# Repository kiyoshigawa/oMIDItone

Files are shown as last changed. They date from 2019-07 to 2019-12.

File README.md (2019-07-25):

This is a project that takes an otamatone (https://otamatone.com/) and hijacks the control using digital potentiometers and a Teensy running USB MIDI libraries to turn it into a MIDI instrument.

The Controller PCB files currently use optoisolators. This design does not work correctly. I manually replaced the optoisolators with darlington NPN transistors, and that led to everything functioning as intended. I plan to revisit the PCB ocne I've tested the advanced features of the board (such as the servo control for opening the mouths, and the addressable LED lighting for the heads) to avoid needing more revisions.

The otamatone has had the touch-pot 'neck' removed and replaced with a connection to two MCP4151 digital potentiometers. I also had to connect two wires to the speaker outputs to get feedback on the frequency being played as the circuit is unstable over time and I could not map a resistance value to a given note accurately and reliably. I ended up removing the original PCBs from the heads and locating them centrally on my controller PCB to make wiring the heads and replacing damaged controllers easier. 

The current revision of the code is working with basic MIDI functionality, including note on, note off, and pitch bend. The pitch bending currently applies to every note currently being played. I intend to change it so that the pitch bend will apply to all the notes only on the MIDI channel it was sent on. This will allow multi-track MIDI files to send each track on a different channel so pitch bend will not effect all the tracks simultaneously. As far as I am aware, there is no way to differentiate tracks once the note messages are sent over MIDI if they are all sending to the same MIDI device, so per-track pitch bend is the best I can hope for given my single MIDI controller setup.

My goal is to finish the design and get all my planned features working with the current PCB, and then release a final version of the code and PCB for anyone who wants to follow in my crazy footsteps.

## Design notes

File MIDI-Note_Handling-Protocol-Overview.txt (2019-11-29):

This is intended to be a general overview explaining the logic in how the oMIDItone handles selecting which MIDI notes to play.

The oMIDItone will make an array of all currently-on notes. This will be updated by MIDI Note-On and Note-Off messages.
Any pitch-bending will apply to all notes without exception.

There are several scenarios that can occur here. Unchanging parameters:
    -There are 127 MIDI notes that can be played, any of which could be on.
    -There are up to 6 oMIDItones available at any given time, sometimes less.
    -You can use oMIDItone.can_play_note() to see if a specific note can be played by any specific head.
    -This results in a set of oMIDItones capable of playing a specific note, from 0-6 possible choices.

So we've got a set of notes, between 0-127, we should be playing, and we've got between 0-6 oMIDItones that can play any given note.

We need to decide which notes to play somehow, and which head to play any given note on.

Scenarios that can arise:
    1. -Notes exist that cannot be played by any heads.
    2. -Less notes than heads, all notes can be played on available heads.
    3. -Less notes than heads, some notes cannot be played on available heads. We will need to select which notes get played on which heads.
    4. -More notes than heads, all within the range of available heads. We will need to select which notes get played on which heads.

We should add a state variable that causes the logic to update only when a note value has changed to save processing time, as this seems like it could get a little complicated.

Solutions:
    1. -Trivially, we can map the max and min notes across all heads and ignore any notes outside this range to save time in for loops constantly checking heads to see what they can play. This should be done during the setup, after all the initializations are complete.
    2. -We check to see that there are only n notes on and >n heads capable of playing all the notes. We need to confirm there is no overlap or multiple notes that can be played on a specific head only and then we can assign heads without worry.
    3. and 4. -This is where things get more complicted. I see there are two paradigms we could follow for these cases to decide how to handle notes:
        A. -The first note that was pressed gets priority over newer notes if a decision has to be made to drop a note.
        B. -The most recently pressed note gets priority over older notes if a decision has to be made to drop a note.
            -B seems to make more sense, as Sodar pointed out that long chord sustains would override the melody bits.

Either way, it sounds like I will need to record the time of the note_on messages somehow so that I can iterate through the notes in the order they were sent to decide which way to operate. Current code only has an array that notes which notes are on or off, it might make sense to do this as an array that holds only the currently-on notes per MIDI, and keeps them in the order they were received. You can also remove notes from the array and shift the remaining notes when receiving note_off commands, adding them to the end of the array. This saves us from having to track the exact time the MIDI messages were received, and keeps things in chronological order.

Also, the chronological array has the advantage that if a note ends and a head that was in use becomes available, a different note can resume even if it was overridden previously.

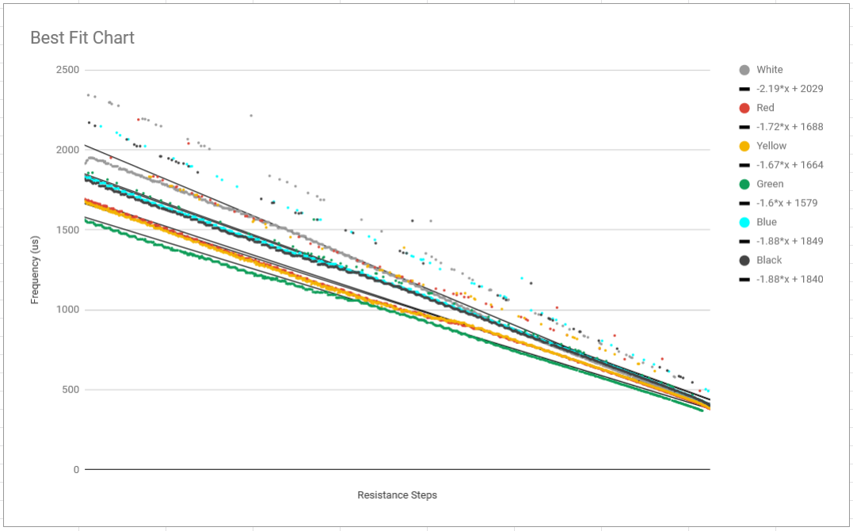
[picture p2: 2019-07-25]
Controller PCB/Reverse Engineering Original Board/Best Fit Chart.PNG

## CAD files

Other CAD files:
Face_Grabber/arm_testing_recover.dwg
Face_Grabber/Light Box Laser Layout.dwg
Face_Grabber/Electronics Backplate.dwg
Face_Grabber/Face-Grabber-FInal.dwg

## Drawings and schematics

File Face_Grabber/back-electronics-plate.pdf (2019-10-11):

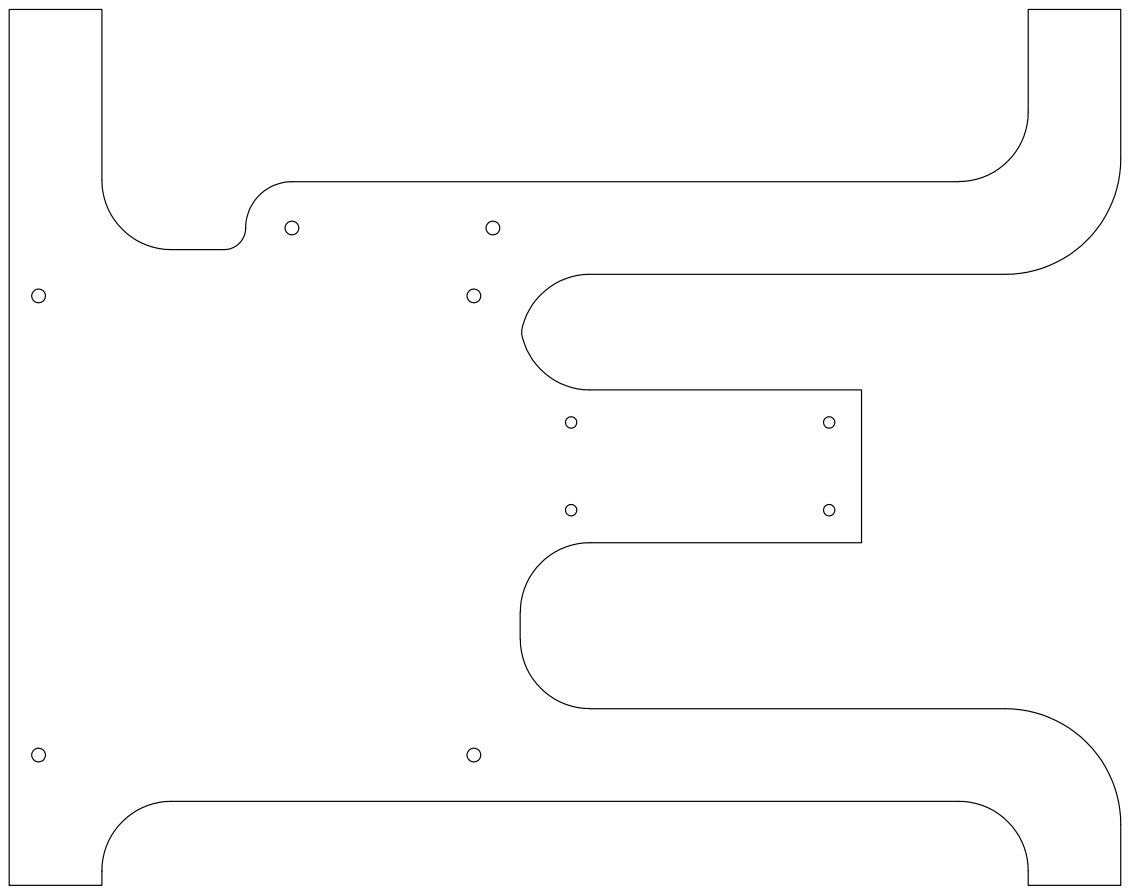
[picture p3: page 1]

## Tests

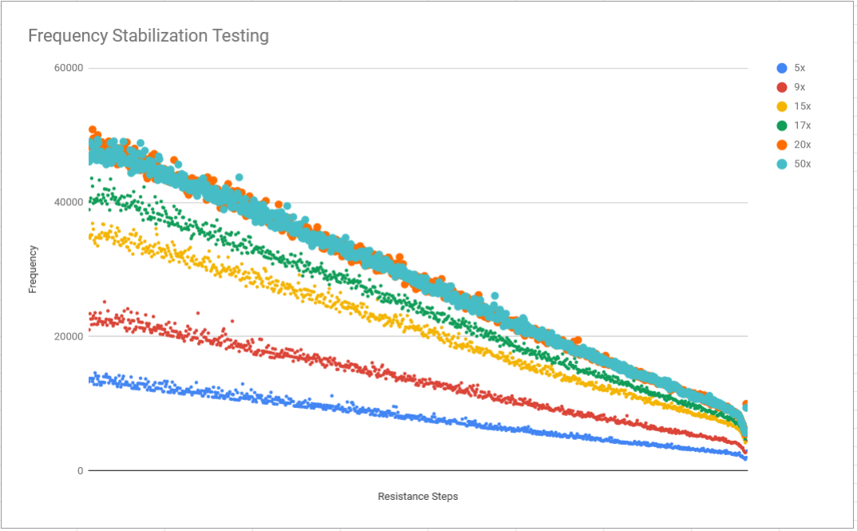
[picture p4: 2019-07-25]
Controller PCB/Reverse Engineering Original Board/Frequency Stabilization Testing.PNG

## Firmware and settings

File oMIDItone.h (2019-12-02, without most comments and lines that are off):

#define OMIDITONE_H
#include <Arduino.h>
#include <SPI.h>
#include "ADC-master/ADC.h"
#include <i2c_t3.h>
#include "Adafruit_PWMServoDriver.h"
#include "lighting_control.h"
#define OMIDITONE_DEBUG
#define FREQUENCY_CORRECTION_DEFAULT_ENABLE_STATE true
#define SERVO_DEFAULT_ENABLE_STATE true
#define NUM_OMIDITONES 6
#define NO_NOTE 128
#define NO_CHANNEL 17
#define NO_RESISTANCE -1
#define NOTE_A 440
#define NUM_MIDI_NOTES 128
#define NUM_MIDI_CHANNELS 16
#define NUM_RESISTANCE_STEPS 765
#define RISING_EDGE_THRESHOLD 50
#define ALLOWABLE_NOTE_ERROR 1
#define DEFAULT_MIDI_PITCH_BEND_SEMITONES 2
#define DEFAULT_MIDI_PITCH_BEND_CENTS 0
#define MAX_PITCH_BEND_SEMITONES 24
#define MAX_PITCH_BEND_CENTS 99
#define ALLOWABLE_FREQUENCY_READING_VARIANCE 50
#define MIN_TIME_BETWEEN_RISING_EDGE_MEASUREMENTS 1
#define NOTE_WAIT_TIME 10
#define TIME_BETWEEN_FREQUENCY_CORRECTIONS 20
#define JITTER 1
#define NUM_FREQ_READINGS 5
#define INIT_MULTIPLIER 17
#define TIME_TO_WAIT_FOR_INIT 2000
#define TIME_TO_WAIT_FOR_STARTUP_TEST_SOUND 100
#define NOTE_TIMEOUT 2000
#define UNREASONABLY_LARGE_MULTIPLIER 2
#define CENTER_PITCH_BEND 0
#define MAX_FREQ 300
#define PCA9685_ADDRESS 0x41
#define PCA9685_FREQUENCY 240
#define PCA9685_OE_PIN 20
#define NUM_LEDS_PER_HEAD 18
#define TIME_BETWEEN_SERVO_MOVEMENTS 16
#define CENT_FREQUENCY_RATIO_MULTIPLIER 1000000
const uint32_t midi_freqs[NUM_MIDI_NOTES] = {122309, 115446, 108968, 102848, 97077, 91633, 86490, 81632, 77053, 72727, 68643, 64792, 61154, 57723, 54484, 51427, 48538, 45814, 43243, 40816, 38525, 36363, 34322, 32396, 30578, 28861, 27242, 25712, 24270, 22907, 21622, 20408, 19262, 18181, 17161, 16198, 15289, 14430, 13621, 12856, 12134, 11453, 10810, 10204, 9631, 9090, 8580, 8099, 7644, 7215, 6810, 6428, 6067, 5726, 5405, 5102, 4815, 4545, 4290, 4049, 3822, 3607, 3405, 3214, 3033, 2863, 2702, 2551, 2407, 2272, 2145, 2024, 1911, 1803, 1702, 1607, 1516, 1431, 1351, 1275, 1203, 1136, 1072, 1012, 955, 901, 851, 803, 758, 715, 675, 637, 601, 568, 536, 506, 477, 450, 425, 401, 379, 357, 337, 318, 300, 284, 268, 253, 238, 225, 212, 200, 189, 178, 168, 159, 150, 142, 134, 126, 119, 112, 106, 100, 94, 89, 84, 79};
const uint32_t cent_frequency_ratios[199] = {1058851, 1058240, 1057629, 1057018, 1056408, 1055798, 1055188, 1054579, 1053970, 1053361, 1052753, 1052145, 1051537, 1050930, 1050323, 1049717, 1049111, 1048505, 1047899, 1047294, 1046689, 1046085, 1045481, 1044877, 1044274, 1043671, 1043068, 1042466, 1041864, 1041262, 1040661, 1040060, 1039459, 1038859, 1038259, 1037660, 1037060, 1036462, 1035863, 1035265, 1034667, 1034070, 1033472, 1032876, 1032279, 1031683, 1031087, 1030492, 1029897, 1029302, 1028708, 1028114, 1027520, 1026927, 1026334, 1025741, 1025149, 1024557, 1023965, 1023374, 1022783, 1022192, 1021602, 1021012, 1020423, 1019833, 1019244, 1018656, 1018068, 1017480, 1016892, 1016305, 1015718, 1015132, 1014545, 1013959, 1013374, 1012789, 1012204, 1011619, 1011035, 1010451, 1009868, 1009285, 1008702, 1008120, 1007537, 1006956, 1006374, 1005793, 1005212, 1004632, 1004052, 1003472, 1002892, 1002313, 1001734, 1001156, 1000578, 1000000, 999423, 998845, 998269, 997692, 997116, 996540, 995965, 995390, 994815, 994240, 993666, 993092, 992519, 991946, 991373, 990801, 990228, 989657, 989085, 988514, 987943, 987373, 986803, 986233, 985663, 985094, 984525, 983957, 983388, 982821, 982253, 981686, 981119, 980552, 979986, 979420, 978855, 978289, 977725, 977160, 976596, 976032, 975468, 974905, 974342, 973779, 973217, 972655, 972093, 971532, 970971, 970410, 969850, 969290, 968730, 968171, 967612, 967053, 966494, 965936, 965379, 964821, 964264, 963707, 963151, 962594, 962039, 961483, 960928, 960373, 959818, 959264, 958710, 958157, 957603, 957050, 956498, 955945, 955393, 954842, 954290, 953739, 953188, 952638, 952088, 951538, 950989, 950439, 949891, 949342, 948794, 948246, 947698, 947151, 946604, 946058, 945511, 944965, 944420};
class oMIDItone {
	public:
		oMIDItone(uint16_t signal_enable_optoisolator, uint16_t speaker_disable_optoisolator, uint16_t cs1, uint16_t cs2, uint16_t feedback, uint16_t servo_l_channel, uint16_t servo_r_channel, uint16_t servo_l_min, uint16_t servo_l_max, uint16_t servo_r_min, uint16_t servo_r_max, uint16_t led_head_array[NUM_LEDS_PER_HEAD], Animation * head_animation);
		void init();
		void update();
		bool note_on(uint16_t note, uint16_t velocity, uint16_t channel);
		void note_off(uint16_t note);
		void set_pitch_bend(int16_t pitch_bend_value, uint8_t pitch_bend_channel);
		void set_max_pitch_bend(uint8_t semitones, uint8_t cents);
		void cancel_pitch_correction();
		void set_servos(uint16_t position);
		bool is_running();
		uint16_t currently_playing_note();
		uint16_t currently_playing_pitch_bend(uint16_t channel);
		void enable_pitch_correction();
		void disable_pitch_correction();
		void enable_servos();
		void disable_servos();
		Animation * animation;
	private:
		bool startup_test();
		void measure_frequency();
		void adjust_frequency();
		bool can_play_note(uint8_t note, int16_t pitch_bend);
		uint32_t pitch_adjusted_frequency(uint8_t note, int16_t pitch_bend);
		void servo_update();
		bool is_rising_edge();
		uint32_t average(unsigned long * array, uint16_t num_elements);
		uint16_t frequency_to_resistance(uint16_t frequency);
		void set_jitter_resistance(uint16_t resistance, uint16_t jitter);
		void set_resistance(uint16_t resistance);
		void set_pot(uint16_t CS_pin, uint16_t command_byte);
		bool had_successful_init;
		bool pitch_correction_is_enabled;
		bool servo_is_enabled;
		uint16_t current_note;
		uint16_t current_velocity;
		uint16_t current_channel;
		uint16_t min_note;
		uint16_t max_note;
		uint32_t measured_freqs[NUM_RESISTANCE_STEPS];
		uint32_t recent_freqs[NUM_FREQ_READINGS];
		uint16_t freq_reading_index;
		uint32_t current_freq;
		uint32_t current_desired_freq;
		uint32_t max_pitch_bend_offset;
		elapsedMicros last_rising_edge;
		elapsedMillis last_adjust_time;
		elapsedMillis last_stabilize_time;
		elapsedMillis note_start_time;
		elapsedMillis startup_stabilization_began;
		elapsedMillis last_frequency_measurement;
		uint16_t last_analog_read;
		int16_t current_oMIDItone_pitch_bend[NUM_MIDI_CHANNELS];
		uint16_t current_resistance;
		uint16_t signal_enable_optoisolator_pin;
		uint16_t speaker_disable_optoisolator_pin;
		uint16_t cs1_pin;
		uint16_t cs2_pin;
		uint16_t analog_feedback_pin;
		ADC *adc = new ADC();
		uint16_t l_channel;
		uint16_t r_channel;
		uint16_t l_min;
		uint16_t l_max;
		uint16_t r_min;
		uint16_t r_max;
		Adafruit_PWMServoDriver servo_controller = Adafruit_PWMServoDriver(PCA9685_ADDRESS);
		elapsedMillis last_servo_update;
		bool pitch_correction_has_been_compromised;
		uint16_t * led_position_array;
};

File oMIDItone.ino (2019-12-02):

/*
Author: kiyoshigawa
Start Date: 2018-03-18
Description:
Took an Otamatone, and replaced the pressure-sensitive variable resistor strip with some MCP4151 50kohm variable pots (2 in series) with a 220Ohm fixed resistor.
Then used a teensy LC MIDI library to control the resistance from the chips over SPI, and connected it to the otamatone, making a oMIDItone.

Update: 2019-03-23: converted the code into a class, rewrote everything to work with the class, can run up to 6 on a Teensy 3.2, only one on a Teensy LC due to lack of RAM.
Update: 2019-03-27: Got all the features working, should be a fully functional MIDI instrument, pending testing of analog read speeds keeping up with higher frequency notes when more than 2 oMIDItones are running. I only have 2 for testing atm, need to buy more.
Update: 2019-09-26: This is now configured (at least initially) for the fully functional v3 PCB, which includes servo face grabbers, LED lighting, and 6 heads. I also added support for per-channel pitch bending, so you can have a channel bend but not all the others with it. Any notes on the bent chanel will be bent as well, though. Working on timing for animation updates, and then I will need to improve the lighting and servo animations. Once those two things are done, I think we can call it stable and mark it as the official release.
Update 2019-11-10: Added MIDI functionality to control various aspects of the oMIDItone using CC messages, and offloaded the MIDI handling to the MIDI_control.h file.

*/

#include "oMIDItone.h"
#include <MIDI.h>
#include <Adafruit_NeoPixel.h>
#include "lighting_control.h"

//this will print messages on system startup and init
#define BOOT_DEBUG

//This will turn on/off the debug note messages when notes are added or removed via MIDI
//#define NOTE_DEBUG

//defines to make the head selection code more readable:
#define AVAILABLE true
#define NOT_AVAILABLE false

//This is the pulse offset in microseconds from the min value of the servo position to the max (i.e. fully open)
#define SERVO_MAX_OFFSET 220

//The next few #defines are for the Adafruit_Neopixel.h library stuff:
#define LED_TOTAL_NUM NUM_LEDS_PER_HEAD*NUM_OMIDITONES
#define LED_DATA_PIN 2
#define LED_COLOR_ORDER NEO_GRB
#define LED_SPEED NEO_KHZ800
#define LED_BRIGHTNESS 255

//This controls the lighting animation timing. 16667 ~= 60Hz, 33333 ~= 30Hz
#define TIME_BETWEEN_LIGHTING_UPDATES 33333

//these are default lighting info for the heads:
#define DEFAULT_BG_MODE LC_BG_RAINBOW_SLOW_ROTATE
#define DEFAULT_FG_MODE LC_FG_NONE
#define DEFAULT_TRIGGER_MODE LC_TRIGGER_COLOR_PULSE

#define DEFAULT_OM1_BG_RAINBOW 16
#define DEFAULT_OM2_BG_RAINBOW 17
#define DEFAULT_OM3_BG_RAINBOW 18
#define DEFAULT_OM4_BG_RAINBOW 19
#define DEFAULT_OM5_BG_RAINBOW 20
#define DEFAULT_OM6_BG_RAINBOW 21
#define DEFAULT_OM1_FG_RAINBOW 1
#define DEFAULT_OM2_FG_RAINBOW 1
#define DEFAULT_OM3_FG_RAINBOW 1
#define DEFAULT_OM4_FG_RAINBOW 1
#define DEFAULT_OM5_FG_RAINBOW 1
#define DEFAULT_OM6_FG_RAINBOW 1
#define DEFAULT_OM1_TRIGGER_RAINBOW 3
#define DEFAULT_OM2_TRIGGER_RAINBOW 5
#define DEFAULT_OM3_TRIGGER_RAINBOW 9
#define DEFAULT_OM4_TRIGGER_RAINBOW 13
#define DEFAULT_OM5_TRIGGER_RAINBOW 7
#define DEFAULT_OM6_TRIGGER_RAINBOW 11

// Pin and other head-specific Definitions
//om#_leds[] arrays are per head ordered from left to right, the first 6 are front leds, the next 6 are the back top, and the final 6 are the back bottom leds
//Red Head:
uint16_t om1_se_pin = 15;
uint16_t om1_sd_pin = 26;
uint16_t om1_cs1_pin = 17;
uint16_t om1_cs2_pin = 16;
uint16_t om1_analog_feedback_pin = A10;
uint16_t om1_l_min = 1390;
uint16_t om1_l_max = om1_l_min + SERVO_MAX_OFFSET;
uint16_t om1_r_min = 1340;
uint16_t om1_r_max = om1_r_min - SERVO_MAX_OFFSET;
uint16_t om1_l_channel = 0;
uint16_t om1_r_channel = 1;
uint16_t om1_leds[NUM_LEDS_PER_HEAD] = {12, 13, 14, 15, 16, 17, 95, 94, 93, 92, 91, 90, 84, 85, 86, 87, 88, 89};
//Yellow Head:
uint16_t om2_se_pin = 33;
uint16_t om2_sd_pin = 25;
uint16_t om2_cs1_pin = 22;
uint16_t om2_cs2_pin = 21;
uint16_t om2_analog_feedback_pin = A11;
uint16_t om2_l_min = 1475;
uint16_t om2_l_max = om1_l_min + SERVO_MAX_OFFSET;
uint16_t om2_r_min = 1430;
uint16_t om2_r_max = om1_r_min - SERVO_MAX_OFFSET;
uint16_t om2_l_channel = 2;
uint16_t om2_r_channel = 3;
uint16_t om2_leds[NUM_LEDS_PER_HEAD] = {23, 22, 21, 20, 19, 18, 59, 58, 57, 56, 55, 54, 48, 49, 50, 51, 52, 53};
//White Head:
uint16_t om3_se_pin = 24;
uint16_t om3_sd_pin = 30;
uint16_t om3_cs1_pin = 3;
uint16_t om3_cs2_pin = 23;
uint16_t om3_analog_feedback_pin = A13;
uint16_t om3_l_min = 1280;
uint16_t om3_l_max = om1_l_min + SERVO_MAX_OFFSET;
uint16_t om3_r_min = 1450;
uint16_t om3_r_max = om1_r_min - SERVO_MAX_OFFSET;
uint16_t om3_l_channel = 4;
uint16_t om3_r_channel = 5;
uint16_t om3_leds[NUM_LEDS_PER_HEAD] = {6, 7, 8, 9, 10, 11, 101, 100, 99, 98, 97, 96, 78, 79, 80, 81, 82, 83};
//Black Head:
uint16_t om4_se_pin = 10;
uint16_t om4_sd_pin = 29;
uint16_t om4_cs1_pin = 9;
uint16_t om4_cs2_pin = 8;
uint16_t om4_analog_feedback_pin = A12;
uint16_t om4_l_min = 1475;
uint16_t om4_l_max = om1_l_min + SERVO_MAX_OFFSET;
uint16_t om4_r_min = 1310;
uint16_t om4_r_max = om1_r_min - SERVO_MAX_OFFSET;
uint16_t om4_l_channel = 6;
uint16_t om4_r_channel = 7;
uint16_t om4_leds[NUM_LEDS_PER_HEAD] = {29, 28, 27, 26, 25, 24, 65, 64, 63, 62, 61, 60, 42, 43, 44, 45, 46, 47};
//Green Head:
uint16_t om5_se_pin = 32;
uint16_t om5_sd_pin = 28;
uint16_t om5_cs1_pin = 7;
uint16_t om5_cs2_pin = 6;
uint16_t om5_analog_feedback_pin = A14;
uint16_t om5_l_min = 1475;
uint16_t om5_l_max = om1_l_min + SERVO_MAX_OFFSET;
uint16_t om5_r_min = 1420;
uint16_t om5_r_max = om1_r_min - SERVO_MAX_OFFSET;
uint16_t om5_l_channel = 8;
uint16_t om5_r_channel = 9;
uint16_t om5_leds[NUM_LEDS_PER_HEAD] = {0, 1, 2, 3, 4, 5, 107, 106, 105, 104, 103, 102, 72, 73, 74, 75, 76, 77};
//Blue Head:
uint16_t om6_se_pin = 31;
uint16_t om6_sd_pin = 27;
uint16_t om6_cs1_pin = 5;
uint16_t om6_cs2_pin = 4;
uint16_t om6_analog_feedback_pin = A0;
uint16_t om6_l_min = 1335;
uint16_t om6_l_max = om1_l_min + SERVO_MAX_OFFSET;
uint16_t om6_r_min = 1410;
uint16_t om6_r_max = om1_r_min - SERVO_MAX_OFFSET;
uint16_t om6_l_channel = 14;
uint16_t om6_r_channel = 15;
uint16_t om6_leds[NUM_LEDS_PER_HEAD] = {35, 34, 33, 32, 31, 30, 71, 70, 69, 68, 67, 66, 36, 37, 38, 39, 40, 41};

//this array controls the type of notes being sent to each head on note_trigger events when they are active:
uint16_t note_trigger_type[NUM_OMIDITONES] = {	DEFAULT_TRIGGER_MODE,
												DEFAULT_TRIGGER_MODE,
												DEFAULT_TRIGGER_MODE,
												DEFAULT_TRIGGER_MODE,
												DEFAULT_TRIGGER_MODE,
												DEFAULT_TRIGGER_MODE};

//these are the Animation objects for the heads above - they will control the animation per-head.
Animation om1_animation = Animation(om1_leds, NUM_LEDS_PER_HEAD,
									(DEFAULT_BG_MODE | DEFAULT_FG_MODE),
									rb_array[DEFAULT_OM1_BG_RAINBOW],
									rb_array[DEFAULT_OM1_FG_RAINBOW],
									rb_array[DEFAULT_OM1_TRIGGER_RAINBOW],
									LC_DEFAULT_REFRESH_RATE);
Animation om2_animation = Animation(om2_leds, NUM_LEDS_PER_HEAD,
									(DEFAULT_BG_MODE | DEFAULT_FG_MODE),
									rb_array[DEFAULT_OM2_BG_RAINBOW],
									rb_array[DEFAULT_OM2_FG_RAINBOW],
									rb_array[DEFAULT_OM2_TRIGGER_RAINBOW],
									LC_DEFAULT_REFRESH_RATE);
Animation om3_animation = Animation(om3_leds, NUM_LEDS_PER_HEAD,
									(DEFAULT_BG_MODE | DEFAULT_FG_MODE),
									rb_array[DEFAULT_OM3_BG_RAINBOW],
									rb_array[DEFAULT_OM3_FG_RAINBOW],
									rb_array[DEFAULT_OM3_TRIGGER_RAINBOW],
									LC_DEFAULT_REFRESH_RATE);
Animation om4_animation = Animation(om4_leds, NUM_LEDS_PER_HEAD,
									(DEFAULT_BG_MODE | DEFAULT_FG_MODE),
									rb_array[DEFAULT_OM4_BG_RAINBOW],
									rb_array[DEFAULT_OM4_FG_RAINBOW],
									rb_array[DEFAULT_OM4_TRIGGER_RAINBOW],
									LC_DEFAULT_REFRESH_RATE);
Animation om5_animation = Animation(om5_leds, NUM_LEDS_PER_HEAD,
									(DEFAULT_BG_MODE | DEFAULT_FG_MODE),
									rb_array[DEFAULT_OM5_BG_RAINBOW],
									rb_array[DEFAULT_OM5_FG_RAINBOW],
									rb_array[DEFAULT_OM5_TRIGGER_RAINBOW],
									LC_DEFAULT_REFRESH_RATE);
Animation om6_animation = Animation(om6_leds, NUM_LEDS_PER_HEAD,
									(DEFAULT_BG_MODE | DEFAULT_FG_MODE),
									rb_array[DEFAULT_OM6_BG_RAINBOW],
									rb_array[DEFAULT_OM6_FG_RAINBOW],
									rb_array[DEFAULT_OM6_TRIGGER_RAINBOW],
									LC_DEFAULT_REFRESH_RATE);

//This is the LED strip object to control all the lighting on the board
Adafruit_NeoPixel strip = Adafruit_NeoPixel(LED_TOTAL_NUM, LED_DATA_PIN, LED_COLOR_ORDER + LED_SPEED);

//this is the lighting controller that will control the lighting updates on the above Adafruit_NeoPixel object's pixels:
LightingControl lc = LightingControl(&strip, LED_BRIGHTNESS);

//this is a timing variable to track lighting updates
elapsedMicros last_lighting_update;

//Using SPI0 on board, MOSI0 = 11, MISO0 = 12, and SCK0 = 13, which will blink the LED as it sends.

//declare the oMIDItone objects:
oMIDItone oms[NUM_OMIDITONES] = {
	oMIDItone(	om1_se_pin, om1_sd_pin, om1_cs1_pin, om1_cs2_pin, om1_analog_feedback_pin, om1_l_channel, 
				om1_r_channel, om1_l_min, om1_l_max, om1_r_min, om1_r_max, om1_leds, &om1_animation),
	oMIDItone(om2_se_pin, om2_sd_pin, om2_cs1_pin, om2_cs2_pin, om2_analog_feedback_pin, om2_l_channel, 
				om2_r_channel, om2_l_min, om2_l_max, om2_r_min, om2_r_max, om2_leds, &om2_animation),
	oMIDItone(om3_se_pin, om3_sd_pin, om3_cs1_pin, om3_cs2_pin, om3_analog_feedback_pin, om3_l_channel, 
				om3_r_channel, om3_l_min, om3_l_max, om3_r_min, om3_r_max, om3_leds, &om3_animation),
	oMIDItone(om4_se_pin, om4_sd_pin, om4_cs1_pin, om4_cs2_pin, om4_analog_feedback_pin, om4_l_channel, 
				om4_r_channel, om4_l_min, om4_l_max, om4_r_min, om4_r_max, om4_leds, &om4_animation),
	oMIDItone(om5_se_pin, om5_sd_pin, om5_cs1_pin, om5_cs2_pin, om5_analog_feedback_pin, om5_l_channel, 
				om5_r_channel, om5_l_min, om5_l_max, om5_r_min, om5_r_max, om5_leds, &om5_animation),
	oMIDItone(om6_se_pin, om6_sd_pin, om6_cs1_pin, om6_cs2_pin, om6_analog_feedback_pin, om6_l_channel, 
				om6_r_channel, om6_l_min, om6_l_max, om6_r_min, om6_r_max, om6_leds, &om6_animation)
};

//this is a variable storing the pitch bend value last received over MIDI:
//Note the teensy library uses a signed pitch bend centered on 0 instead of the MIDI standard of centering on 8192.
int16_t current_pitch_bend[NUM_MIDI_CHANNELS];

//this is an array that tracks whether a note is currently on or off.
uint8_t current_note_array[NUM_MIDI_NOTES];

//this will note the velocity that corresponds to the note array above.
uint8_t current_velocity_array[NUM_MIDI_NOTES];

//this will note the channel that corresponds to the note array above.
uint8_t current_channel_array[NUM_MIDI_NOTES];

//this tracks how many notes are in the array.
uint8_t num_current_notes = 0;

//this is a bool to let the controller know when it needs to reassign notes to the heads.
bool note_has_changed = false;

//this is a bool to let the controller know when it needs to reassign pitch bend to the heads.
bool pitch_has_changed = false;

//this updates all the heads when MIDI CC pitch bend messages are received:
bool pitch_bend_range_has_changed = false;

//these globals store the value of the pitch range in semitones and cents
uint8_t MIDI_max_pitch_bend_num_semitones = DEFAULT_MIDI_PITCH_BEND_SEMITONES;
uint8_t MIDI_max_pitch_bend_num_cents = DEFAULT_MIDI_PITCH_BEND_CENTS;

//This tracks the current head so the iteration isn't always in the same place.
int head_offset = 0;

//this controls whether lighting is enabled or not
bool lighting_is_enabled = true;

//this controls whether note on messages send triggers to the head that plays the note:
bool note_trigger_is_enabled = true;

//this is an array that is sorted in the order of the least recently used heads to the most recently used heads
//it allows for the least recently used heads to be selected first when deciding whish head will play a note
uint8_t head_order_array[NUM_OMIDITONES];
//this stores the state of the head order array until all notes are off, then it is pushed into the actual head order array.
uint8_t pending_head_order_array[NUM_OMIDITONES];

//Start the hardware MIDI:
MIDI_CREATE_INSTANCE(HardwareSerial, Serial1, MIDI);

//this is just a quick function to print the note array with some formatting:
void print_current_note_array(){
	#ifdef NOTE_DEBUG
		if(num_current_notes > 0){
			Serial.print("Notes: [");
			if(num_current_notes > 0){
				for(int i=0; i<num_current_notes-1; i++){
					Serial.print(current_note_array[i]);
					Serial.print(", ");
				}
			}
			Serial.print(current_note_array[num_current_notes-1]);
			Serial.println("]");
		} else {
			Serial.println("Notes: []");
		}
	#endif
}

//This will check to see if a note is in the current_note_array and return the position of the note if it finds one, or return NO_NOTE if it does not.
int check_note(uint8_t note){
	//Iterate through the array, and return the note position if it is found.
	if(num_current_notes == 0){
		return NO_NOTE;
	} else {
		for(int i=0; i<num_current_notes; i++){
			if(current_note_array[i] == note){
				return i;
			}
		}
		//if no note is found, return NO_NOTE;
		return NO_NOTE;
	}
}

//This will add a new note to the end of the current_note_array, or relocate the note to the end if it is already in the array.
//It will also add a velocity value corresponding to that note to the current_velocity_array.
void add_note(uint8_t note, uint8_t velocity, uint8_t channel){
	uint8_t note_position = check_note(note);
	//if the note isn't already in the array, put it at the end of the array.
	if(note_position == NO_NOTE){
		current_note_array[num_current_notes] = note;
		current_velocity_array[num_current_notes] = velocity;
		current_channel_array[num_current_notes] = channel;
		num_current_notes++;
	} else {
		//if it is in the array, put the note at the end and bend everything back down to where the note used to be.
		for(int i=note_position; i<num_current_notes; i++){
			current_note_array[i] = current_note_array[i+1];
			current_velocity_array[i] = current_velocity_array[i+1];
			current_channel_array[i] = current_channel_array[i+1];
		}
		current_note_array[num_current_notes-1] = note;
		current_velocity_array[num_current_notes-1] = velocity;
		current_channel_array[num_current_notes-1] = channel;
	}
}

//If a note is in the current_note_array, this will remove it, and the corresponding velocity will be removed from the current_velocity_array
//and then it will bend the rest of the values down to fill in the gap.
void remove_note(uint8_t note){
	uint8_t note_position = check_note(note);
	//if the note is in the note array, remove it and bend down any other notes.
	if(note_position != NO_NOTE){
		for(int i=note_position; i<num_current_notes; i++){
			current_note_array[i] = current_note_array[i+1];
			current_velocity_array[i] = current_velocity_array[i+1];
			current_channel_array[i] = current_channel_array[i+1];
		}
		num_current_notes--;
	} else {
		//Do nothing
	}
	//need to get the head to immediately stop playing the note as well:
	for(int i=0; i<NUM_OMIDITONES; i++){
		if(oms[i].currently_playing_note() == note){
			oms[i].note_off(note);
		}
	}

	//and finally change the head_order_array to match the pending_head_order_array when all notes are off
	if(num_current_notes <= 0){
		for(int i=0; i<NUM_OMIDITONES; i++){
			head_order_array[i] = pending_head_order_array[i];
		}
	}
}

//this function moves the head in question to the end of the head_order_array, and shuffles the remaining heads down into its place.
void pending_head_order_to_end(uint8_t head_number){
	//don't need to iterate to the last one, because if the head_number is in the last position already, we're good
	for(int i=0; i<NUM_OMIDITONES-1; i++){
		if(pending_head_order_array[i] == head_number){
			//set the current position to the next head in line
			pending_head_order_array[i] = pending_head_order_array[i+1];
			//and move the head in question down the line until it's in the last place
			pending_head_order_array[i+1] = head_number;
		}
	}
}

//this is a function to send commands to the oMIDItones connected to this controller based on the note_status_array and current_pitch_bend
void update_oMIDItones(){
	//First set the pitch for all the running oMIDItones.
	//this can just iterate through all of them in order, since it doesn't require load balancing like note_on.
	if(pitch_has_changed){
		for(int i=0; i<NUM_OMIDITONES; i++){
			for(int channel=0; channel<NUM_MIDI_CHANNELS; channel++){
				oms[i].set_pitch_bend(current_pitch_bend[channel], channel);
			}
		}
		pitch_has_changed = false;
	}
	//this will set the pitch bend range whenever it is changed:
	if(pitch_bend_range_has_changed){
		for(int i=0; i<NUM_OMIDITONES; i++){
			for(int channel=0; channel<NUM_MIDI_CHANNELS; channel++){
				oms[i].set_max_pitch_bend(MIDI_max_pitch_bend_num_semitones, MIDI_max_pitch_bend_num_cents);
			}
		}
		pitch_bend_range_has_changed = false;
	}
	//only update if a note has changed state:
	//TIM: Reevaluate how heads are assigned to noted. Maybe switch to iterating through the heads and assigning them the first note available instead of the current way?
	if(note_has_changed){
		//we need a couple variables that we can use to iterate through all the heads in the right order.
		bool head_state[NUM_OMIDITONES];
		for(int i=0; i<NUM_OMIDITONES; i++){
			//mark all heads as available initially
			head_state[i] = AVAILABLE;
		}
		//only do this if there are notes to be played.
		if(num_current_notes > 0){
			//iterate through the active notes so that we can see if any heads are available to play them.
			//we need to go from the end of the list backwards.
			for(int n=num_current_notes-1; n>=0; n--){
				//iterate through the array of unassigned heads.
				for(int h=0; h<NUM_OMIDITONES; h++){
					//only check the notes if the head hasn't been assigned.
					if(head_state[h] == AVAILABLE){
						if(oms[head_order_array[h]].note_on(current_note_array[n], current_velocity_array[n], current_channel_array[n])){;
							//trigger a lighting update on the head
							#ifdef NOTE_DEBUG
								Serial.print("H");
								Serial.print(head_order_array[h]);
								Serial.print(": Playing Note ");
								Serial.println(current_note_array[n]);
							#endif
							if(note_trigger_is_enabled){
								oms[head_order_array[h]].animation->trigger_event(note_trigger_type[head_order_array[h]]);
							}
							//remove the head from the unassigned heads array
							head_state[h] = NOT_AVAILABLE;
							//move the head to the end of the head_order_array
							pending_head_order_to_end(head_order_array[h]);
							//break the head for loop so no other heads try to play the same note:
							break;
						} //note_on
					} //head_state == AVAILABLE
				} //head for loop
			} //note for loop
			//reset the state variable once everything has been tried/assigned.
			note_has_changed = false;
		} //num_current_notes > 0
	} //note has changed

	//Finally, this will update the oMIDItone objects:
	for(int i=0; i<NUM_OMIDITONES; i++){
		oms[i].update();
	}
}

void setup(){
	#ifdef BOOT_DEBUG
		Serial.begin(9600);
		delay(5000); //wait for serial
		Serial.println("Welcome to oMIDItone.");
		Serial.println("Beginning initialization - this may take several minutes...");
	#endif

	//initialize the pitch bend to the default value of no pitch bend:
	for(int i=0; i<NUM_MIDI_CHANNELS; i++){
		current_pitch_bend[i] = CENTER_PITCH_BEND;
	}
	pitch_has_changed = true;

	//initialize the head order array and pending_head_order_array to be 0-5 in order:
	for(int i=0; i<NUM_OMIDITONES; i++){
		head_order_array[i] = i;
		pending_head_order_array[i] = i;
	}

	//set up the lighting controller with the animations
	lc.init();
	for(int i=0; i<NUM_OMIDITONES; i++){
		lc.add_animation(oms[i].animation);
	}
	lc.update();

	//init the om objects - This is going to take a while - like several minutes:
	for(int i=0; i<NUM_OMIDITONES; i++){
		//init the head
		oms[i].init();
	}

	//call out MIDI functions
	usbMIDI.setHandleNoteOff(OnNoteOff);
	usbMIDI.setHandleNoteOn(OnNoteOn);
	usbMIDI.setHandlePitchChange(OnPitchChange);
	usbMIDI.setHandleControlChange(OnControlChange);

	//Hardware MIDI init.
	MIDI.begin(MIDI_CHANNEL_OMNI);

	#ifdef BOOT_DEBUG
		Serial.println("Init Complete, awaiting MIDI input.");
	#endif
}

void loop(){

	//This will read for MIDI notes and start/stop the notes based on MIDI input:
	usbMIDI.read();
	//This will check the hardware MIDI channels and start/stop the notes based on MIDI input.
	read_hardware_MIDI();
	//This will decide which oMIDItone to use for which note, and update the status.
	update_oMIDItones();
	//this will update all lighting functions on a regular basis
	//update_lighting(); //old - delete once lc is working
	if(lighting_is_enabled){
		int lighting_data_was_sent = lc.update();
		if(lighting_data_was_sent == LC_STRIP_WRITTEN){
			for(int h=0; h<NUM_OMIDITONES; h++){
				oms[h].cancel_pitch_correction();
			}
		}
	}
}

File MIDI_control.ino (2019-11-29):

/*
This contains all the MIDI handling functions for the oMIDItone.
It has both the hardware MIDI interpreting, as well as the USB MIDI interpreting
Make sure to update the MICI_CCV values if new lighting modes are added to lighting control.h
Otherwise the new modes will not work with the oMIDItone, since they are not explicitly allowed in the handle_cc() function
*/

#define MIDI_DEBUG

//these define the background lighting modes which correspond to the MIDI note values. They should be sent as the CC Value
//make sure to update as lighting controller is updated with new modes
#define MIDI_CCV_BG_TYPE_OFF 1
#define MIDI_CCV_BG_TYPE_SOLID 2
#define MIDI_CCV_BG_TYPE_SLOW_FADE 3
#define MIDI_CCV_BG_TYPE_RAINBOW_FIXED 4
#define MIDI_CCV_BG_TYPE_RAINBOW_SLOW_ROTATE 5

//this is used when an invalid code is sent:
#define DEFAULT_BG MIDI_CCV_BG_TYPE_RAINBOW_SLOW_ROTATE

//these define the foreground lighting modes which correspond to the MIDI note values. They should be sent as the CC Value
//Note that the FG numbers will be bit shifted 8 bits over to comply with the lighting controller values. Verify that the numbers used correspond correctly.
//make sure to update as lighting controller is updated with new modes
#define MIDI_CCV_FG_TYPE_NONE 0
#define MIDI_CCV_FG_TYPE_MARQUEE_SOLID_FIXED 1
#define MIDI_CCV_FG_TYPE_MARQUEE_SOLID 2
#define MIDI_CCV_FG_TYPE_MARQUEE_SLOW_FADE_FIXED 3
#define MIDI_CCV_FG_TYPE_MARQUEE_SLOW_FADE 4
#define MIDI_CCV_FG_TYPE_VU_METER 5

//this is used when an invalid code is sent:
#define DEFAULT_FG MIDI_CCV_FG_TYPE_NONE

//These define which trigger to use when receiving a MICI_CC_OM#_TRIGGER command. They should be sent as the CC Value
//make sure to update as lighting controller is updated with new modes
#define MIDI_CCV_TR_TYPE_BG 0
#define MIDI_CCV_TR_TYPE_FG 1
#define MIDI_CCV_TR_TYPE_COLOR_PULSE 2
#define MIDI_CCV_TR_TYPE_COLOR_PULSE_SLOW_FADE 3
#define MIDI_CCV_TR_TYPE_COLOR_PULSE_RAINBOW 4
#define MIDI_CCV_TR_TYPE_COLOR_SHOT 5
#define MIDI_CCV_TR_TYPE_COLOR_SHOT_SLOW_FADE 6
#define MIDI_CCV_TR_TYPE_COLOR_SHOT_RAINBOW 7
#define MIDI_CCV_TR_TYPE_FLASH 8
#define MIDI_CCV_TR_TYPE_FLASH_SLOW_FADE 9
#define MIDI_CCV_TR_TYPE_FLASH_RAINBOW 10

//this is used when an invalid code is sent:
#define DEFAULT_TRIGGER MIDI_CCV_TR_TYPE_COLOR_PULSE

//These define the MIDI control codes to change lighting and animation effects:

//standard MIDI codes that may be useful to implement go here.
#define MIDI_CC_ALL_SOUND_OFF 120
#define MIDI_CC_RESET_ALL_CONTROLLERS 121
#define MIDI_CC_ALL_NOTES_OFF 123

//this is used as the default note value for pitsh bend when a CC 121 is sent.
#define DEFAULT_PITCH_BEND 0

//this is used for setting the number of semitones for MIDI pitch bending
#define MIDI_CC_PITCH_BEND_RANGE_COARSE 6
//this is used for setting the number of cents off of the semitones above for MIDI pitch bending
#define MIDI_CC_PITCH_BEND_RANGE_FINE 38

//the pitch bend range will only work if both CC100 and CC101 are set to 0
#define MIDI_CC_REGISTERED_PARAMETER_LSB 100
#define MIDI_CC_REGISTERED_PARAMETER_MSB 101

//these are defines used for MIDI RPN messages to determine what type of RPN message is being sent:
//so far only pitch bend adjust is implemented
#define MIDI_RPN_PITCH_BEND_ADJUST_MODE 0
#define MIDI_RPN_FINE_TUNING_MODE 1
#define MIDI_RPN_COARSE_TUNING_MODE 2
#define MIDI_RPN_TUNING_PROGRAM_CHANGE_MODE 3
#define MIDI_RPN_TUNING_BANK_SELECT_MODE 4
#define MIDI_RPN_MODULATION_DEPTH_RANGE_MODE 5

#define RPN_NO_MODE 127

//this resets the MCU and forces a new tune-up:
#define MIDI_CC_HARD_RESET 9

//These control whether major features are enabled or disabled. A value of 0 disables, all other values enable
#define MIDI_CC_PITCH_CORRECTION_ENABLE 14
#define MIDI_CC_NOTE_TRIGGER_ENABLE 15
#define MIDI_CC_LIGHTING_ENABLE 20
#define MIDI_CC_SERVO_ENABLE 21
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

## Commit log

2019-03-26 Initial Class Commit - freq measure is broken
    [MCP4151-Pin-Swap-B.Cu.gbr, MCP4151-Pin-Swap-B.Mask.gbr, MCP4151-Pin-Swap-B.SilkS.gbr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]
2019-03-27 Stabilization Working with fast ADC lib
2019-07-25 I don't know how to git.
    [Face_Grabber.dwg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]
2019-10-11 Several lighting modes, including VU_meter work
    [Electronics Backplate.dwg, Face-Grabber-FInal.dwg, Face_Grabber.dwg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]
2019-11-06 Before I mess with frequency correction...
    [lighting_control.cpp, lighting_control.h, oMIDItone.ino]
2019-11-10 Fixed some bugs, left others...
    [oMIDItone.ino]
2019-11-10 Bug Fixes for FG and BG overriding themselves.
    [MIDI_control.ino, lighting_control.cpp, lighting_control.h]
2019-11-17 Add Servo Position Control when Seros are Disabled
2019-11-25 lighting all working, pitch bending still broken
    [MIDI_control.ino, lighting_control.cpp, lighting_control.h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]
2019-11-26 Pitch bending works, but is too slow.
    [MIDI_control.ino, oMIDItone.h, oMIDItone.ino]
2019-11-29 formatting cleanup, pitch still wonky
